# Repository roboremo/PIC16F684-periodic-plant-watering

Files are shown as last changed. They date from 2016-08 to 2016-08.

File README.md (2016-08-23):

# PIC16F684-periodic-plant-watering
Plant watering system using the PIC16F684 microcontroller.
The MCU commands a 12V solenoid valve to open with specific period, and close after a specific interval.
The period and interval can be configured over Bluetooth using Android phone with RoboRemo app.
The settings are stored in the EEPROM memory of the PIC, so they don't get lost at power OFF.

video: https://www.youtube.com/watch?v=9LrbubgdCc8

Commands:

"get\n" - get parameter values (p = period, i = open interval)  
"time\n" - get up time (how many seconds passed since system was powered)  
"set p [n]\n" - set period, in seconds. Example: "set p 300\n" - valve wil open every 5 minutes  
"set i [n]\n" - set the open interval, in seconds. Example: "set i 20\n" - valve will stay open for 20 seconds  
"open\n" - manually open valve (for test)  
"close\n" - manually close valve (for test)  

The push button is used to turn ON the Bluetooth module, which is off by default, to reduce the power consumption. The system turns off the Bluetooth module automatically after 30s if not receiving any command.

The Bluetooth module used in this project is the BlueSMiRF, configured to 9600 baud.

The blue LED blinks every 2s to signal that system is running.

Current draw (with Bluetooth OFF and valve OFF) is about 6mA.  
That gives a battery life of about 30 days (with 5Ah 12V battery)

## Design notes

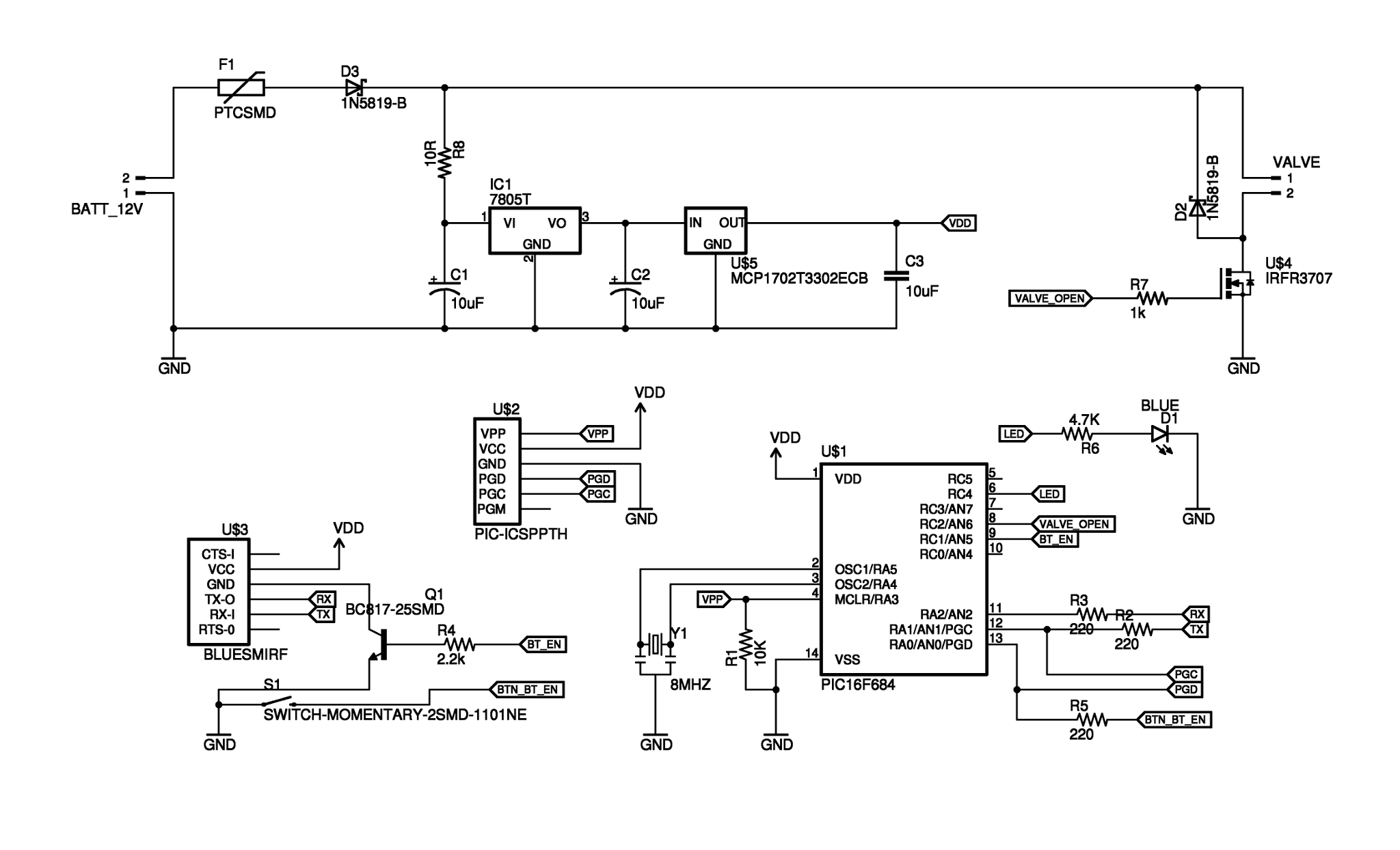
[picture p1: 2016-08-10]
schematic.png

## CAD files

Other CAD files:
684-plant-watering.X/dist/default/production/684-plant-watering.X.production.obj

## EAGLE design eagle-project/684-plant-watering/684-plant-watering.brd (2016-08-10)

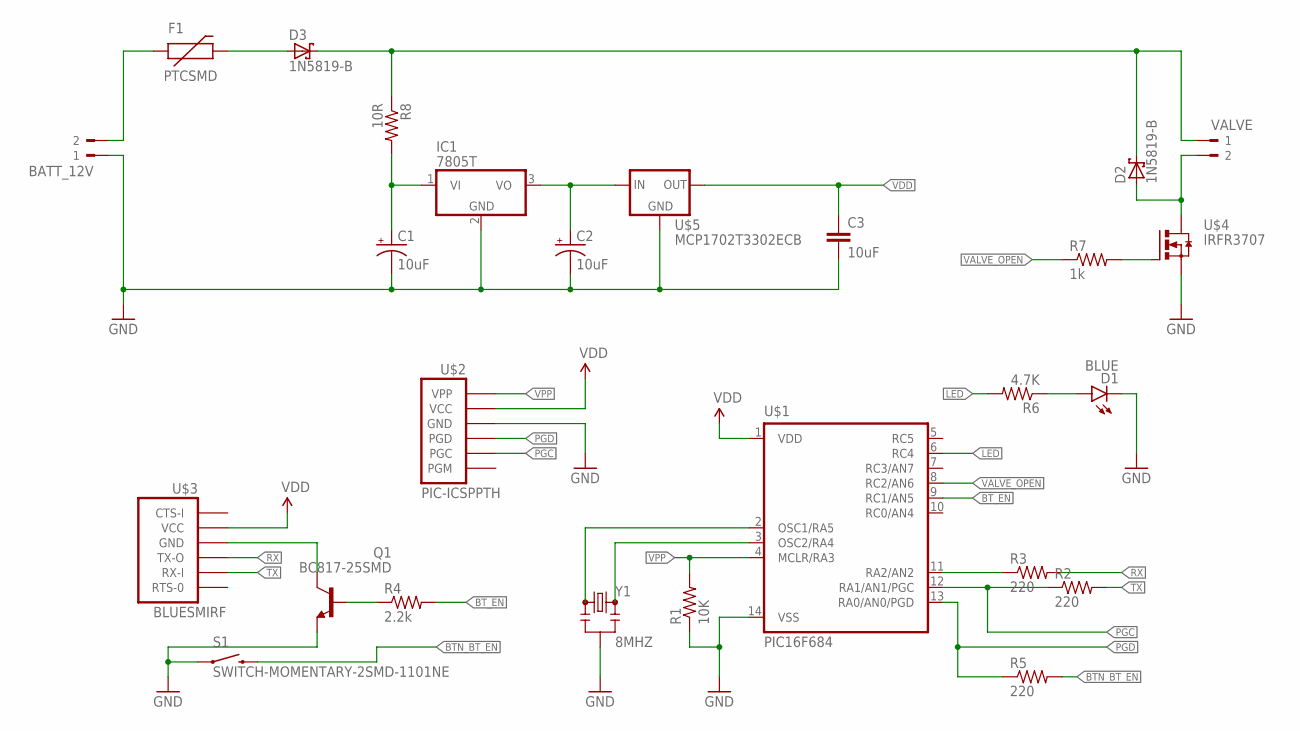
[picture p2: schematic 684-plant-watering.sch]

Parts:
BATT_12V: 180-2
C1, C2: 10uF; CPOL-RADIAL-10UF-25V
C3: 10uF; 0603-CAP
D1: BLUE; LED-1206
D2, D3: 1N5819-B; DO41-7.6
F1: PTCSMD; PTC-1206
IC1: 7805T; TO220H
Q1: BC817-25SMD; SOT23-BEC
R1: 10K; 0603-RES
R2, R3, R5: 220; 0603-RES
R4: 2.2k; 0603-RES
R6: 4.7K; 0603-RES
R7: 1k; 0207/10
R8: 10R; 0309/12
S1: SWITCH-MOMENTARY-2SMD-1101NE; TACTILE-SWITCH-1101NE
U$1: PIC16F684; SO14
U$2: PIC-ICSPPTH; MOLEX-1X6
U$3: BLUESMIRF; 1X06
U$4: IRFR3707; TO252
U$5: MCP1702T3302ECB; SOT23
VALVE: 180-2
Y1: 8MHZ; RESONATOR-SMD

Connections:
BTN_BT_EN: R5.2, S1.2
BT_EN: R4.2, U$1.9 (RC1/AN5)
GND: BATT_12V.1, C1.2 (-), C2.2 (-), C3.2, D1.C, IC1.2 (GND), Q1.E, R1.1, S1.1, U$1.14 (VSS), U$2.4 (GND), U$4.3 (S), U$5.1 (GND), Y1.2
LED: R6.2, U$1.6 (RC4)
unnamed: R3.1, U$1.11 (RA2/AN2)
unnamed: Q1.C, U$3.3 (GND)
unnamed: Q1.B, R4.1
unnamed: D1.A, R6.1
unnamed: D2.A, U$4.4 (D), VALVE.2
unnamed: BATT_12V.2, F1.1
unnamed: R7.2, U$4.1 (G)
unnamed: D2.C, D3.C, R8.1, VALVE.1
unnamed: U$1.2 (OSC1/RA5), Y1.1
unnamed: C1.1 (+), IC1.1 (VI), R8.2
unnamed: C2.1 (+), IC1.3 (VO), U$5.3 (IN)
unnamed: U$1.3 (OSC2/RA4), Y1.3
unnamed: D3.A, F1.2
PGC: R2.1, U$1.12 (RA1/AN1/PGC), U$2.2 (PGC)
PGD: R5.1, U$1.13 (RA0/AN0/PGD), U$2.3 (PGD)
RX: R3.2, U$3.4 (TX-O)
TX: R2.2, U$3.5 (RX-I)
VALVE_OPEN: R7.1, U$1.8 (RC2/AN6)
VDD: C3.1, U$1.1 (VDD), U$2.5 (VCC), U$3.2 (VCC), U$5.2 (OUT)
VPP: R1.2, U$1.4 (MCLR/RA3), U$2.6 (VPP)

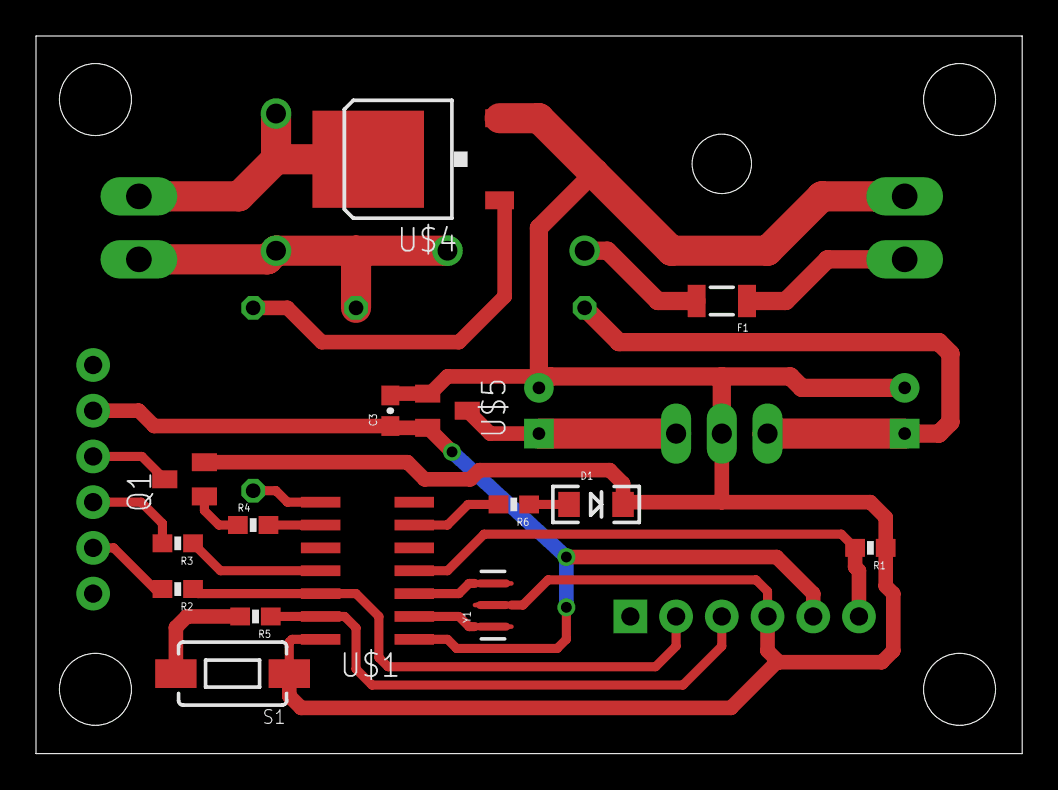
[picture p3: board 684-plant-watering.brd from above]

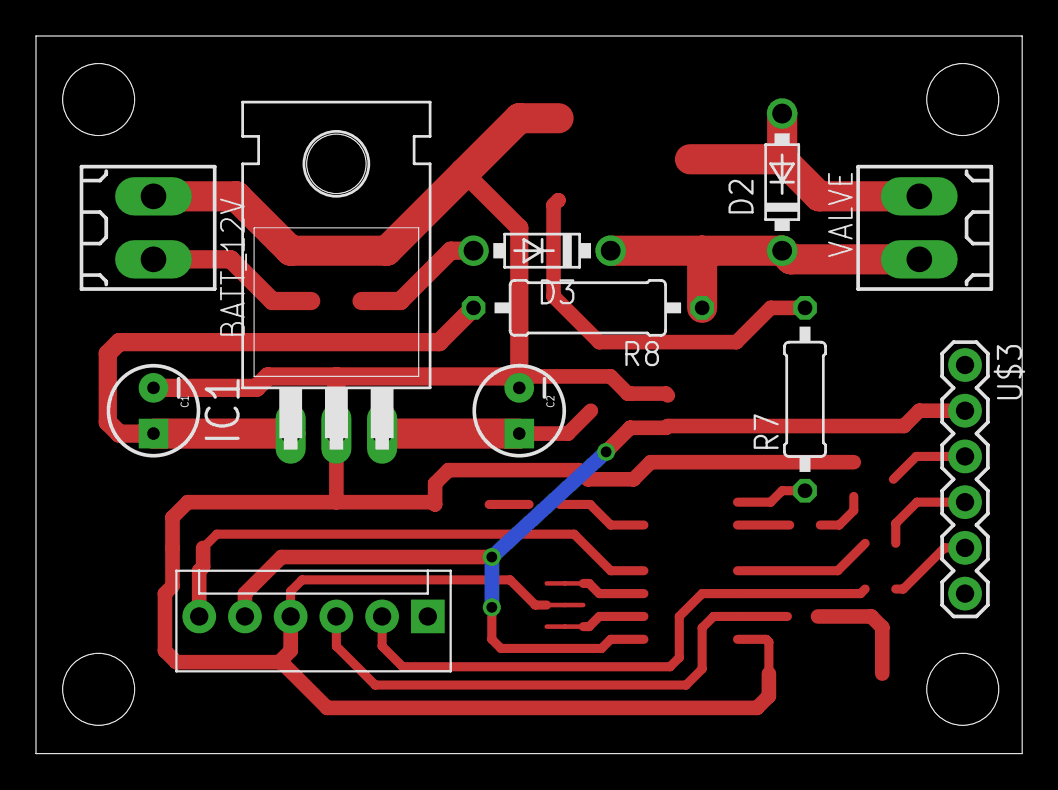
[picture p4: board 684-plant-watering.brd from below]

Board: 2 copper layers, 54.8 x 39.9 mm, 26 parts (11 on the bottom side), 24 nets.

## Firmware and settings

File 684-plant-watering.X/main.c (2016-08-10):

// code written by RoboRemo
// http://www.roboremo.com
// please don't remove this :)


#include "pic16f684.h"

#include <stdint.h>
#include <stdbool.h>
#include <stdlib.h>
#define int1_t bit


//#define forceCR



// PIC16F684 Configuration Bit Settings


// CONFIG
#pragma config FOSC = HS
#pragma config WDTE = OFF       // Watchdog Timer Enable bit (WDT disabled)
#pragma config PWRTE = ON       // Power-up Timer Enable bit (PWRT enabled)
#pragma config MCLRE = OFF      // MCLR Pin Function Select bit (MCLR pin function is digital input, MCLR internally tied to VDD)
#pragma config CP = OFF         // Code Protection OFF
#pragma config CPD = OFF        // Data Memory Code Protection OFF
#pragma config BOREN = OFF      // Brown Out Detect (BOR disabled)
#pragma config IESO = OFF       // Internal External Switchover bit (Internal External Switchover mode is disabled)
#pragma config FCMEN = OFF      // Fail-Safe Clock Monitor Enabled bit (Fail-Safe Clock Monitor is disabled)


//    Vdd       |--v--|  Vss
//    RA5       |     |  RA0 / AN0
//    RA4 / AN3 | 16F |  RA1 / AN1
//    RA3       | 684 |  RA2 / AN2 / INT
//    RC5       |     |  RC0 / AN4
//    RC4       |     |  RC1 / AN5
//    RC3 / AN7 |-----|  RC2 / AN6


#define led PORTCbits.RC4
#define btEn PORTCbits.RC1
#define valveOpen PORTCbits.RC2

#define btnBTen PORTAbits.RA0
#define uartTx PORTAbits.RA1
#define uartRx PORTAbits.RA2


#include "soft_uart_8_9600.c"   // 9600 baud for 8 MHz
#include "eeprom.c"
#include "plant_watering_params.c"


uint8_t btEnCounter = 0; // counter to turn off Bluetooth after a few seconds

#define btEnSeconds 30 // keep ON for 30 seconds after last command

void initPORTS() {
    
    CMCON0 = 0b00000111; // comparators off
    ANSEL = 0b00000000;   // all digital
    
    TRISA = 0b11111101;
    OPTION_REGbits.nRAPU = 0; // global PORTA pull-ups enabled
    WPUA = 0b00000101; // Rx and btnBTen pull-ups enabled
    
    uartTx = 1; // idle
    
    TRISC = 0b11101001;
    
    led = 0; // OFF
    btEn = 0;
    valveOpen = 0;
    
}



void openValve() {
    valveOpen = 1;
}


void closeValve() {
    valveOpen = 0;
}



uint8_t tCounter;
uint32_t sec; // overflows after 136 years :)

uint8_t cmd[32];
uint8_t cmdIndex;


uint8_t cmdStartsWith(uint8_t *st) {
  for(uint8_t i=0; ; i++) {
    if(st[i]==0) return 1;
    if(cmd[i]==0) return 0;
    if(cmd[i]!=st[i]) return 0;
  }
}



void exeCmd() { 


  if( cmdStartsWith("get") ) {
    showParams();
  }
  
  if( cmdStartsWith("tim") ) {
      puts("up time: "); putn(sec); putc('s'); putLF();
  }
  

  if( cmdStartsWith("open") ) {
    openValve();
  }

  if( cmdStartsWith("close") ) {
    closeValve();
  }

  if( cmdStartsWith("set ") ) { // set p(eriod) / set i(nterval)
    int32_t val = atol(cmd+6);
    updateParam(cmd[4], val);
    showParams();
    //sec = 0;
  }
  
  btEnCounter = btEnSeconds;

}


uint8_t cmdReady;

void main(void) {
    
    uint8_t c;
    uint32_t r;

    initPORTS();
   
    
    //OSCCONbits.IRCF0 = 1;
    //OSCCONbits.IRCF1 = 1;
    //OSCCONbits.IRCF2 = 1;  // FOR INTERNAL 8 MHz
    
    cmdIndex = 0;
    initParams();
    
    //puts("hi :)\n");
    
    T2CONbits.TMR2ON = 0;
    T2CONbits.T2CKPS = 0b11; // prescaler = 16, T2 CLK = 125 KHz (for 8 MHz)
    T2CONbits.TOUTPS = 9; // 1:10 postscale
    PR2 = 249; // 0.05 KHz -> 20 ms interrupt (period is PR2+1)
    TMR2 = 0;
    
    //puts("PR2 = "); putn(PR2); putc('\n');
    
    
    tCounter = 0;
    sec = 0;
    T2CONbits.TMR2ON = 1; // Start timer
    
    
    // configure external interrupt:
    IOCAbits.IOC2 = 1; // interrupt only for RA2
    INTCONbits.RAIE = 1; // enable interrupt
    INTCONbits.RAIF = 0; // clear flag
    
    // enable global interrupts:
    INTCONbits.GIE = 1;
    
    
    
    cmdReady = 0;
    

    while(1) {
        
        if(cmdReady) {  // set by isr
            exeCmd();  // execute the command
            cmdIndex = 0; // reset the cmdIndex
            cmdReady = 0;
        }
        
        
        if(!btnBTen) { // "Bluetooth enable" button pressed
            btEn = 1; // enable Bluetooth
            btEnCounter = btEnSeconds; // disable after a few seconds
        }
        
        
        if(PIR1bits.TMR2IF) {
            PIR1bits.TMR2IF = 0;
            tCounter++;
            if(tCounter==50) {
                tCounter = 0;
                sec++;
                
                
                
                /////////////////////////////////////////////////////////
                
                
                //if(sec==20) {
                //    puts("hi :)\n"); // for debug
                //}
                
                if(btEnCounter) {
                    btEnCounter--;
                    if(btEnCounter==0) {
                        btEn = 0; // disable Bluetooth (to save power)
                    }
                }
                
                
                
                /*if(sec==params.p) {
                    openValve();
                }

                if(sec==params.p + params.i) {
                    closeValve();
                    sec = params.i; // to start from there
                }*/
                
                r = sec % params.p;
                
                if(r == 0) {
                    openValve();
                }

                if(r == params.i) {
                    closeValve();
                    //sec = params.i; // to start from there
                }
                
                /////////////////////////////////////////////////////////
                
            }
            
            
            if( (sec & 0x01) == 0) {
                if(tCounter==0) led = 1;
                if(tCounter==5) led = 0;
            }
            
            //led = 1 - led;
        }
        
    }
    
}


uint8_t c;

void interrupt isr() {  // interrupt serving routine
    
    // external interrupt used as kbhit for software serial
    
    c = getc();

    if(c=='\n' || c=='\r') {
      cmd[cmdIndex] = 0;
      cmdReady = 1;
    } else {      
      cmd[cmdIndex] = c;
      if(cmdIndex<31) cmdIndex++;
    }
    
    INTCONbits.RAIF = 0; // clear flag
    
}

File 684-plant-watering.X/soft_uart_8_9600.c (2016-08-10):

// code written by RoboRemo
// http://www.roboremo.com
// please don't remove this :)


// NOTE:
// delays are tuned for 9600 baud (for 8MHz XTAL)
// compiled with XC8 v1.34 free
// other versions may have different optimization, so you may need to re-tune


uint8_t kbhit() {
    return (uartRx==0);
}

uint8_t getc() {
    uint8_t res, a, i, j;
    uint16_t wait;

    res = 0;

    wait = 0;

    while(uartRx==1) {} // may happen when called directly


    // debug:
    //LATBbits.LATB0 = 1;

    //delay_104us();   // for 9600
    for(j=0; j<19; j++) {
        asm ("NOP");
    } 
    asm ("NOP");
    asm ("NOP");
    asm ("NOP");
    asm ("NOP");
    asm ("NOP");
    asm ("NOP");
    //asm ("NOP");
    //asm ("NOP");

    for(i=0; i<8; i++) {

        for(j=0; j<8; j++) {
            asm ("NOP");
        }
        asm ("NOP");
        asm ("NOP");
        
        res = res << 1;
        res += uartRx;
        
        for(j=0; j<9; j++) {
            asm ("NOP");
        }
    }



    a = res;
    res = 0;

    for(i=0; i<8; i++) {
        res = res << 1;
        res += a%2;
        a = a >> 1;
    }




    while(uartRx==0) {}

    return res;

}


void putc(uint8_t data) {
    uint8_t i, j;

#ifdef forceCR
    if(data=='\n') data = '\r';
#endif

    uartTx = 0;
    //delay_104us();  // for 9600
    
    for(j=0; j<19; j++) {
        asm ("NOP");
    } 
    asm ("NOP");
    asm ("NOP");
    asm ("NOP");
    asm ("NOP");
    //asm ("NOP");
    //asm ("NOP");
    //asm ("NOP");
    //asm ("NOP");
    

    for(i=0; i<8; i++) {
        
        uartTx = data & 0x01;
        data = data >> 1;
        
        for(j=0; j<16; j++) {
            asm ("NOP");
        }
    }

    uartTx = 1;
    
    
    for(j=0; j<18; j++) {
        asm ("NOP");
    }
}



void puts(const uint8_t *s) {
    uint8_t i;

    for(i=0; s[i]!=0; i++) {
        putc(s[i]);
        
        //delay_100us();
        //delay_100us();
    }
}



void putn(int32_t n) {  // -99999999 to 99999999
    uint8_t z;
    uint8_t dig, i;
    const uint32_t decaShift[] = {10000000, 1000000, 100000, 10000, 1000, 100, 10};

    if(n<0) {
        n = -n;
        putc('-');
    }

    z = 1;
    
    for(i=0; i<7; i++) {
        dig = ((n/decaShift[i])%10)+'0';
        if(z==1 && dig=='0') {}
        else {z = 0; putc(dig);}
    }
    
    dig = ((n)%10)+'0'; 
    //if(z==1 && dig=='0') {}
    //else {z = 0; uartPutc(dig);}
    putc(dig);

}


void putLF() {   // things that you start to do when out of memory
    putc('\n');
}

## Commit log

2016-08-10 added MPLABX project
    [684-plant-watering.X.production.obj, proteus-design.DSN]
2016-08-10 added schematic image and Eagle project
    [684-plant-watering.brd, 684-plant-watering.sch]

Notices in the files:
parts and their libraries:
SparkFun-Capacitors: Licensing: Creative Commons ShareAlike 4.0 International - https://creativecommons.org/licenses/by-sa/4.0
